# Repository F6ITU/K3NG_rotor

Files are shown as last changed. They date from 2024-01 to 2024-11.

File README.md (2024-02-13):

# K3NG_rotor
Yet another K3NG rotator controler pcb

This implementation is based on an Arduino Mega board and a pair of 4x relay boards to drive an AZ-EL antenna system.

Most basic functions are directly driven via Molex KK 254 connectors (up/down, right/left, lcd display output, GPS input, *
I2C extensions... etc). All other "vacant" gpio could be used via solderpads. 

Board could be powered from 8 to 15V 

Source code and wiki should be downloaded at 

https://github.com/k3ng/k3ng_rotator_controller

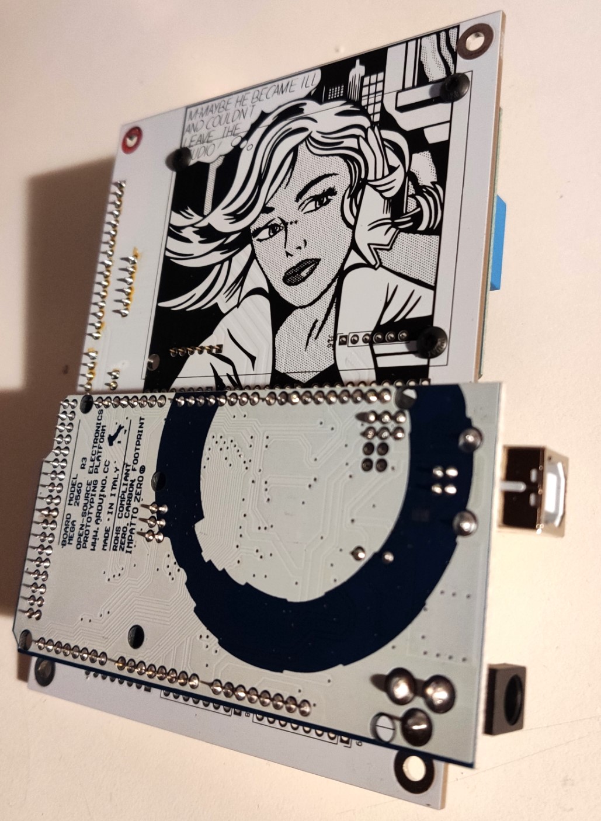
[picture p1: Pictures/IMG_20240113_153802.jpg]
K3NG rotator, component side


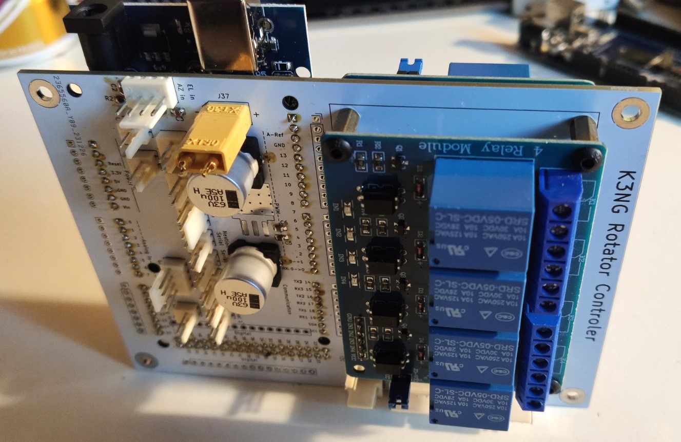
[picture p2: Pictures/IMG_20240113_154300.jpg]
K3NG rotator, bottom side


# Notes de montage

* Les barrettes de contact au pas de 2,54 doivent être soudées après les avoir insérées dans les connecteur gpio de l’Arduino. La série de brasure doit donc être effectuée avec le module MCU en place, lequel servira ainsi de gabarit d’alignement pour les broches. Sans cette précaution, il sera quasiment impossible d’installer l’Arduino sur la carte. 

* Le régulateur de tension doit être le circuit à souder avant tout autre composant. Les deux principaux condensateurs de filtrage sont très proche du 7805 et gêneraient la brasure ce celui-ci s’il était monté a posteriori

* Tous les connecteurs Molex kk254 ne sont pas nécessairement à installer. C’est le cas notamment des entrées gpio « serial » de 0 à 3, qui peuvent être remplacés par de simples jumpers les reliant aux sorties des périphériques installés. Cela permet de choisir sur quel port seront reliés les modules  gps ou Nextion s’il y a lieu

* Toutes les E/S de l’Arduino sont doublées par une rangée de contacts au pas de 2,54, laissant libre toute possibilité d’ajouts de modules exotiques. 

* Les modules « 4 relais » disponibles sur Amazon ou AliExpress sont généralement livrés avec un connecteur « broches  carte à fils » au pas de 2,54mm orientés vers le dessus de la carte. Il est nécessaire de les dessouder et de les remplacer par un connecteur identique, mais soudé « coté piste ». Le shield K3NG doit, pour sa part, être équipé d’un connecteur femelle « carte à carte » pour recevoir la ou les cartes relais en « piggy back ». 

* Deux cartes relais peuvent être installées pour piloter une paire de moteurs azimut/élévation. Prévoir deux entretoises d’une hauteur équivalente aux connecteurs de liaison. 

* ATTENTION : les relais sont commandés « 2 à 2 », soit pour assurer une coupure courants forts, soit pour être utilisés en inverseur (un contact ouvert et un contact fermé au repos, et lycée de Versailles au travail). Cette configuration est notamment nécessaire pour commander les rotor Kantronic/Yaesu/Toyomura d’ancienne génération (split phase ou à phase divisée)

 * Une BOM interactive est disponible sur ce Github dans le répertoire BOM du même métal

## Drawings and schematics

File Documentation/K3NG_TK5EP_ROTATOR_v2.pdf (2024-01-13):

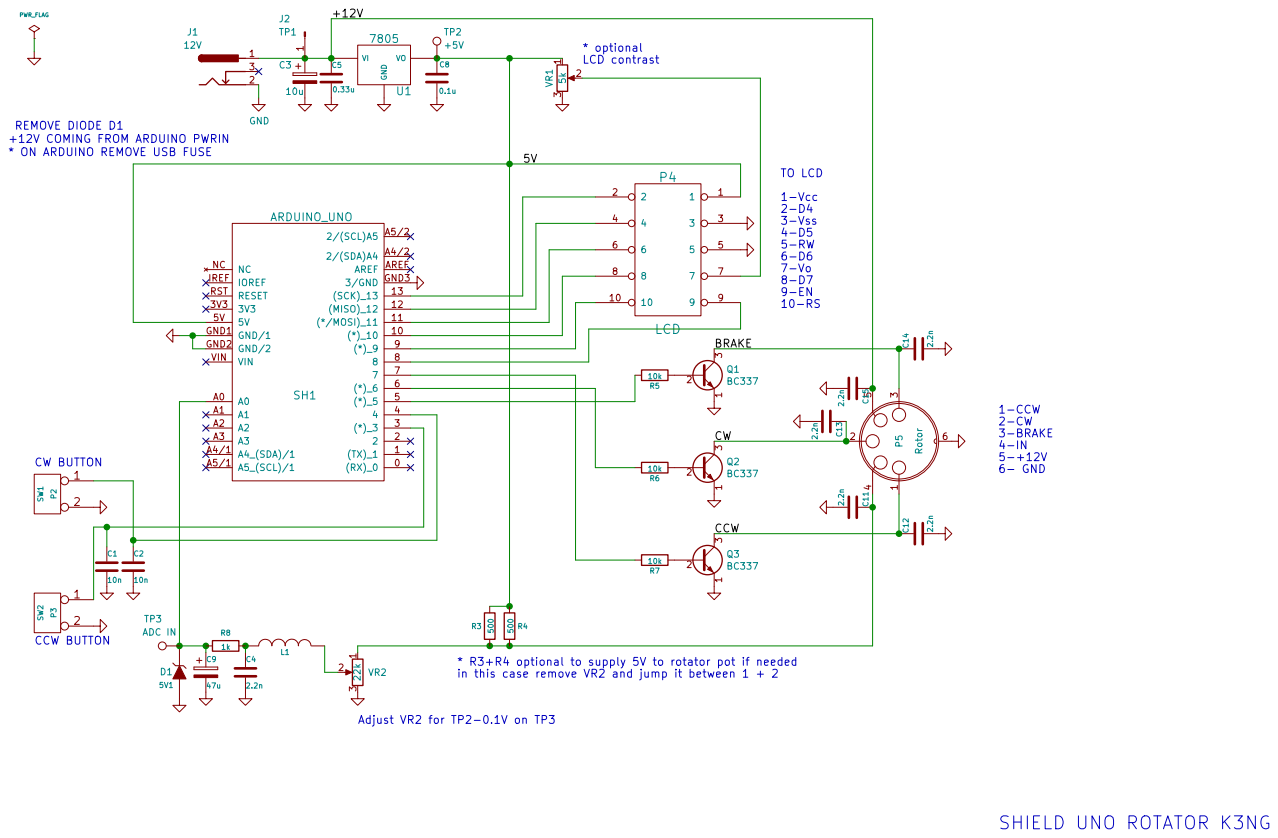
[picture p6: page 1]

+12V COMING FROM ARDUINO PWRIN
* ON ARDUINO REMOVE USB FUSE

ARDUINO_UNO

in this case remove VR2 and jump it between 1 + 2

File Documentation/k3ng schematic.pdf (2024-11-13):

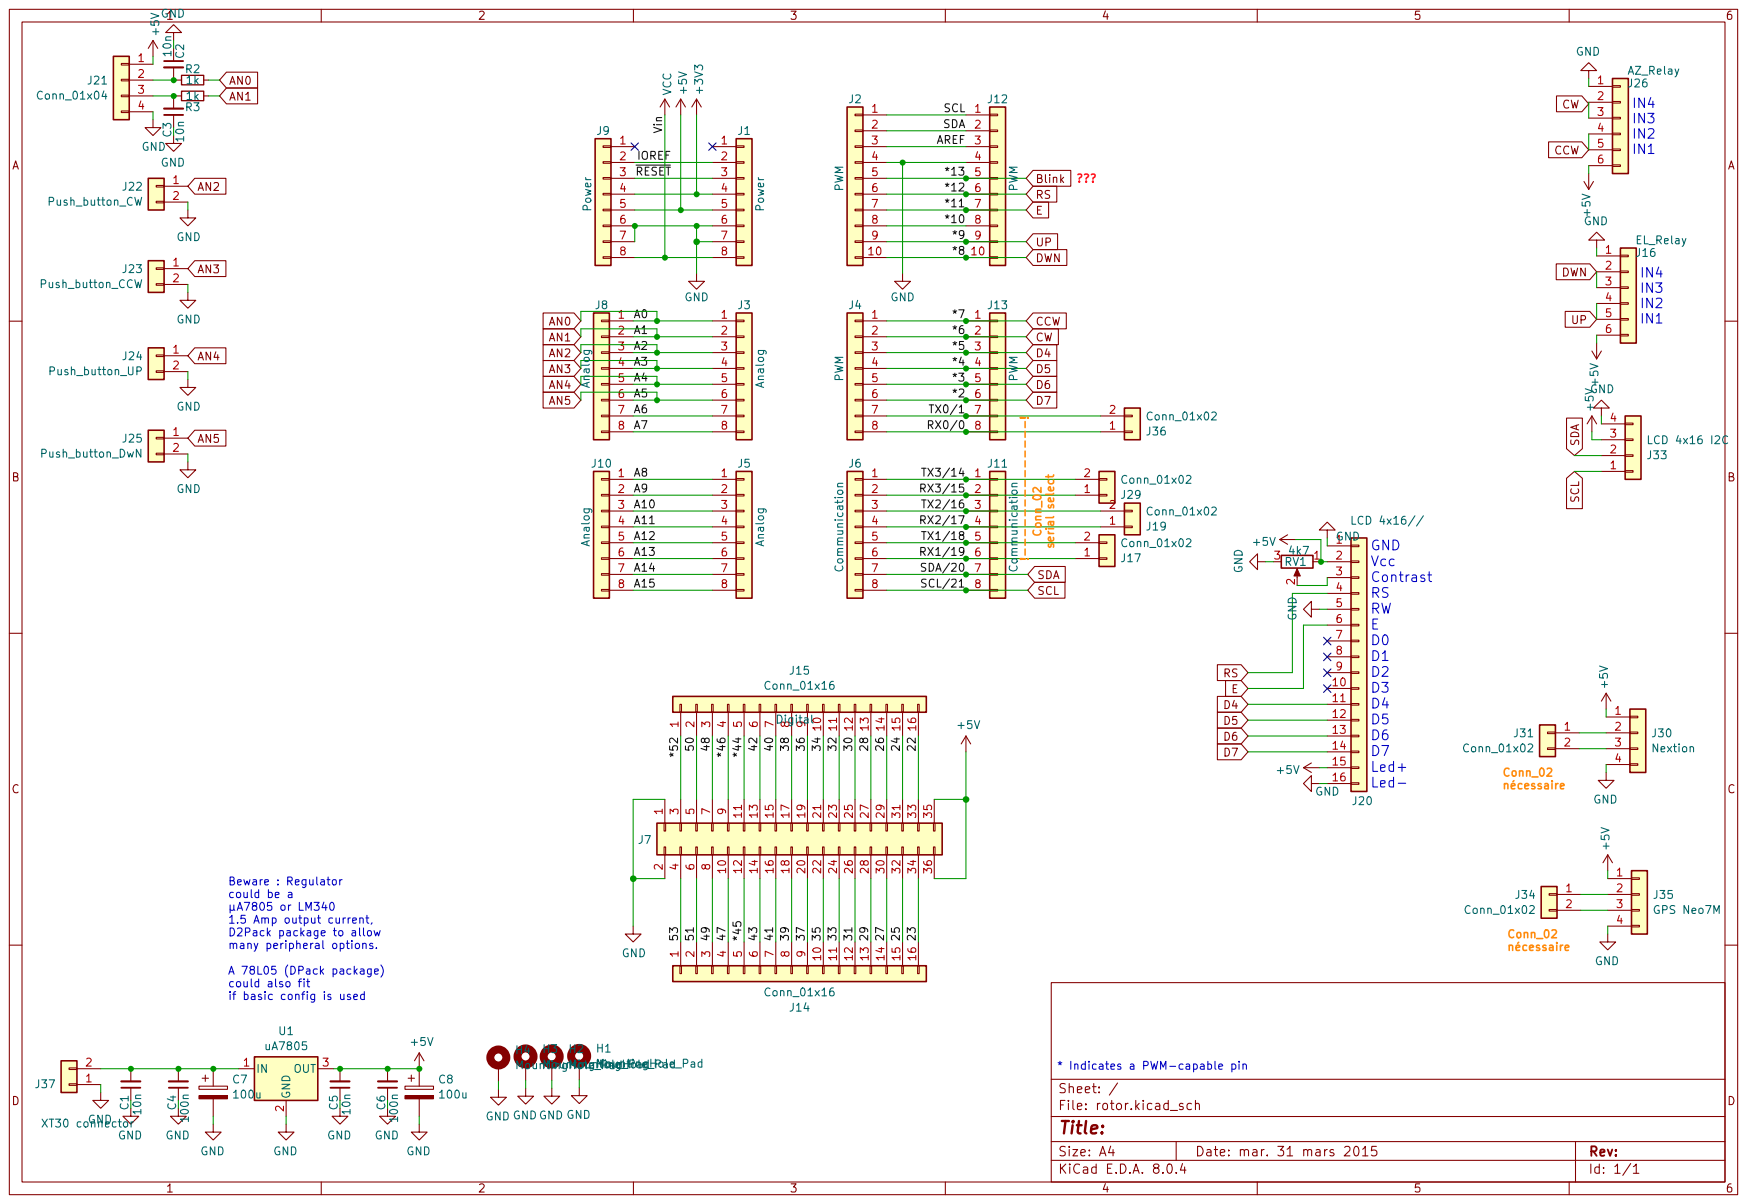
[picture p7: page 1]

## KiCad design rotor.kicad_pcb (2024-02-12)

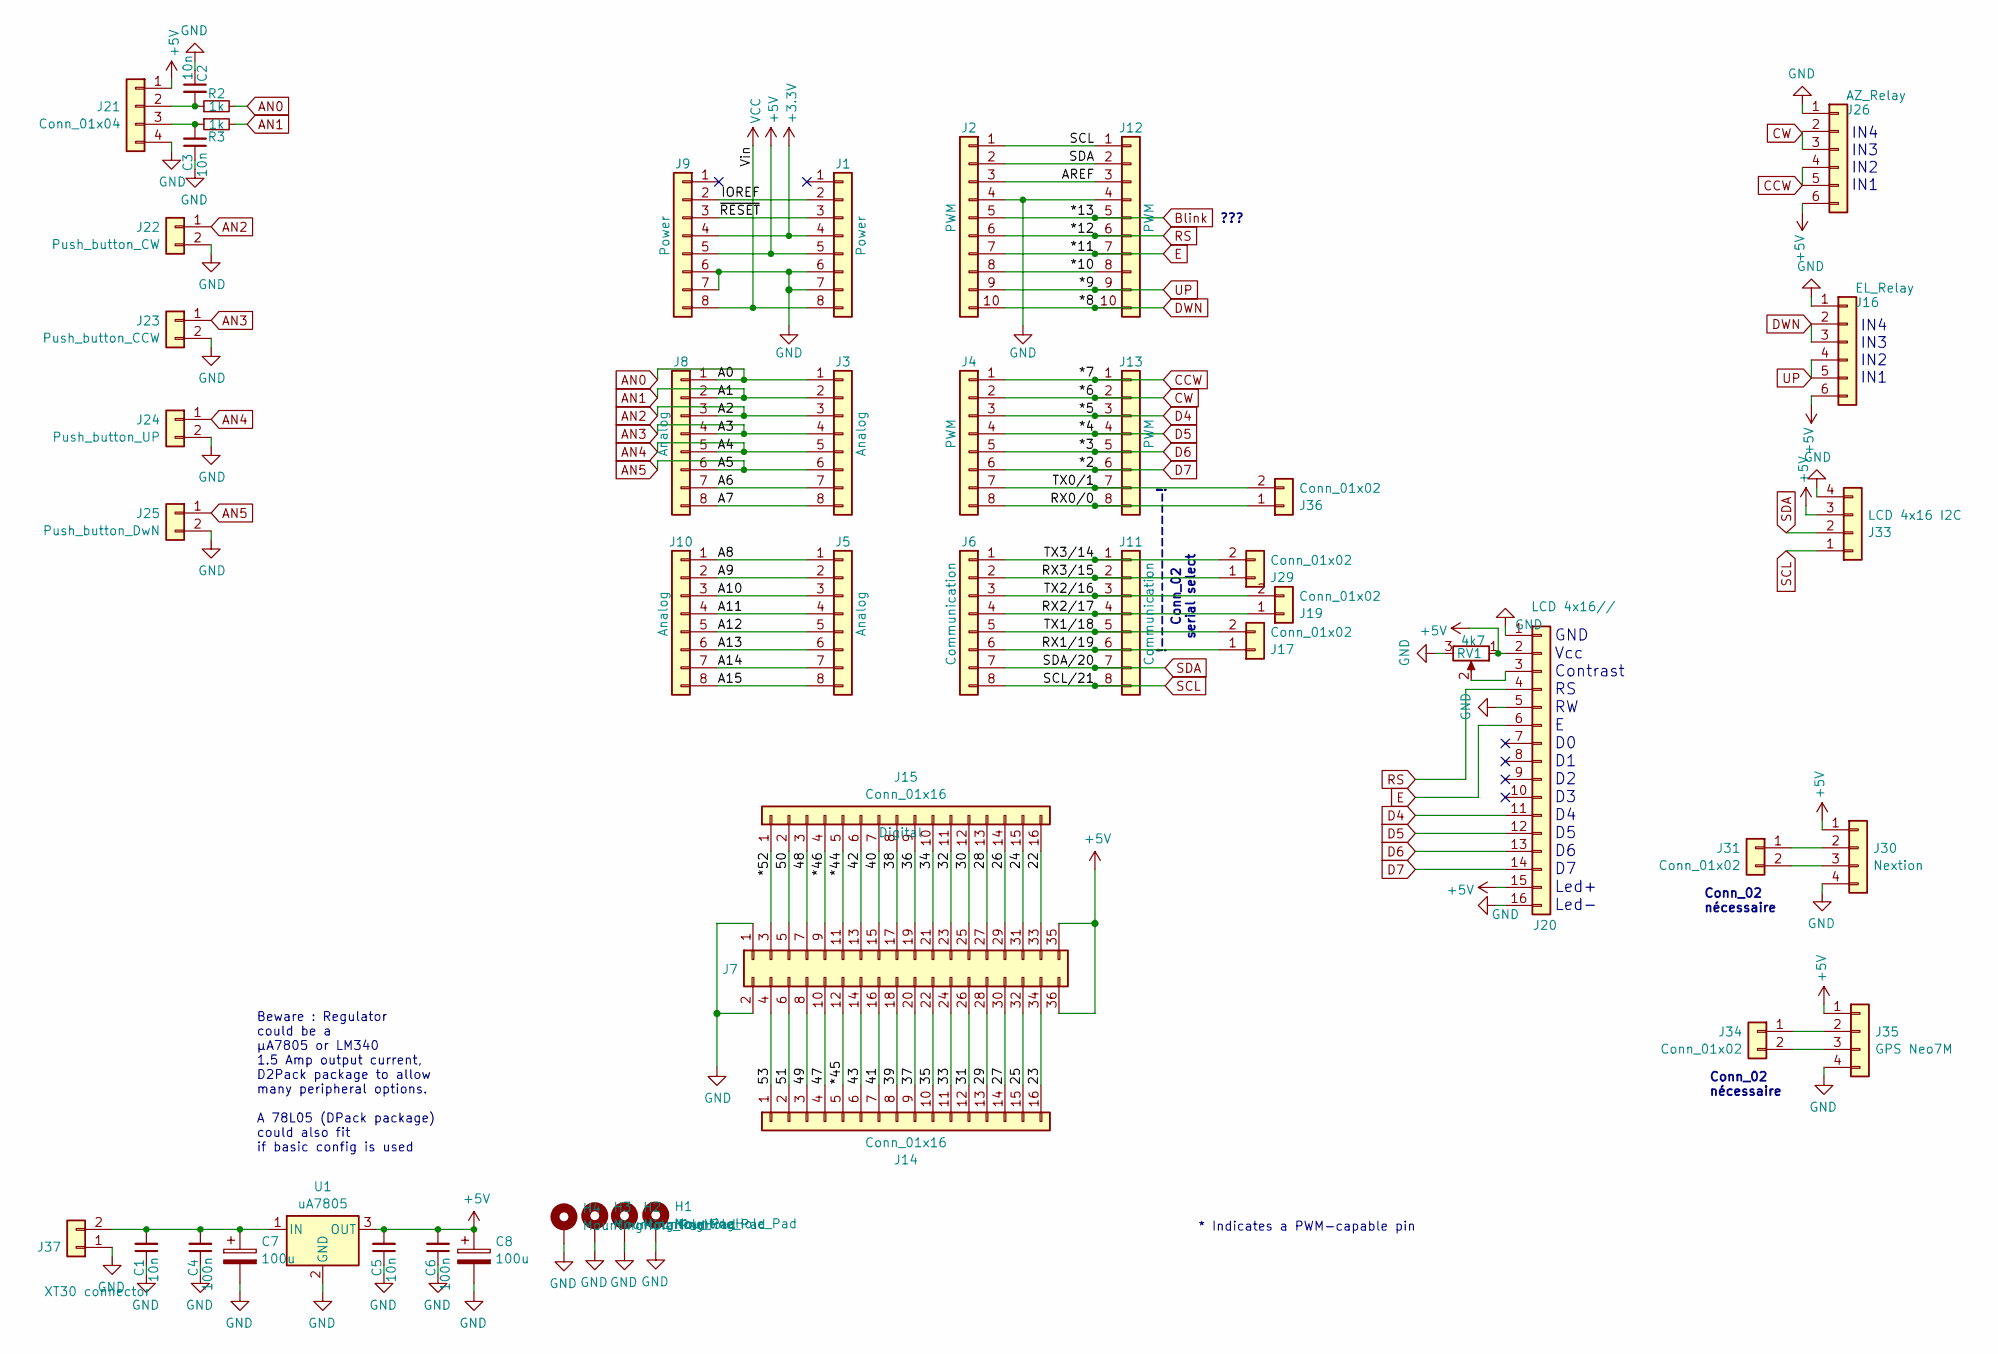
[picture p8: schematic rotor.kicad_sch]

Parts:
C1, C2, C3, C5: 10n; C_0805_2012Metric_Pad1.18x1.45mm_HandSolder
C4, C6: 100n; C_0805_2012Metric_Pad1.18x1.45mm_HandSolder
C7, C8: 100u; CP_Elec_10x12.6
H1, H2, H3, H4: MountingHole_Pad; MountingHole_3.5mm_Pad
J1, J9: Power; PinSocket_1x08_P2.54mm_Vertical
J2, J12: PWM; PinSocket_1x10_P2.54mm_Vertical
J3, J8: Analog; PinHeader_1x08_P2.54mm_Vertical
J4, J13: PWM; PinSocket_1x08_P2.54mm_Vertical
J5, J10: Analog; PinSocket_1x08_P2.54mm_Vertical
J6, J11: Communication; PinSocket_1x08_P2.54mm_Vertical
J7: Digital; PinSocket_2x18_P2.54mm_Vertical
J14, J15: Conn_01x16; PinHeader_1x16_P2.54mm_Vertical
J16: EL_Relay; PinSocket_1x06_P2.54mm_Vertical
J17, J19, J29, J31, J34, J36: Conn_01x02; Molex_KK-254_AE-6410-02A_1x02_P2.54mm_Vertical
J20: LCD 4x16//; Molex_KK-254_AE-6410-16A_1x16_P2.54mm_Vertical
J21: Conn_01x04; Molex_KK-254_AE-6410-04A_1x04_P2.54mm_Vertical
J22: Push_button_CW; Molex_KK-254_AE-6410-02A_1x02_P2.54mm_Vertical
J23: Push_button_CCW; Molex_KK-254_AE-6410-02A_1x02_P2.54mm_Vertical
J24: Push_button_UP; Molex_KK-254_AE-6410-02A_1x02_P2.54mm_Vertical
J25: Push_button_DwN; Molex_KK-254_AE-6410-02A_1x02_P2.54mm_Vertical
J26: AZ_Relay; PinSocket_1x06_P2.54mm_Vertical
J30: Nextion; Molex_KK-254_AE-6410-04A_1x04_P2.54mm_Vertical
J33: LCD 4x16 I2C; Molex_KK-254_AE-6410-04A_1x04_P2.54mm_Vertical
J35: GPS Neo7M; Molex_KK-254_AE-6410-04A_1x04_P2.54mm_Vertical
J37: XT30 connector; AMASS_XT30U-F_1x02_P5.0mm_Vertical
R2, R3: 1k; R_0805_2012Metric_Pad1.20x1.40mm_HandSolder
RV1: 4k7; Potentiometer_Bourns_TC33X_Vertical
U1: uA7805; TO-263-3_TabPin2

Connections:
+3V3: J1.4, J9.4
+5V: C5.2, C6.2, C8.1, J1.5, J7.35, J7.36, J9.5, J16.6, J20.2, J20.15, J21.1, J26.6, J30.1, J33.3, J35.1, RV1.1, U1.3 (OUT)
/22: J7.33, J15.16
/23: J7.34, J14.16
/24: J7.31, J15.15
/25: J7.32, J14.15
/26: J7.29, J15.14
/27: J7.30, J14.14
/28: J7.27, J15.13
/29: J7.28, J14.13
/30: J7.25, J15.12
/31: J7.26, J14.12
/32: J7.23, J15.11
/33: J7.24, J14.11
/34: J7.21, J15.10
/35: J7.22, J14.10
/36: J7.19, J15.9
/37: J7.20, J14.9
/38: J7.17, J15.8
/39: J7.18, J14.8
/40: J7.15, J15.7
/41: J7.16, J14.7
/42: J7.13, J15.6
/43: J7.14, J14.6
/47: J7.10, J14.4
/48: J7.7, J15.3
/49: J7.8, J14.3
/50: J7.5, J15.2
/51: J7.6, J14.2
/53: J7.4, J14.1
/*10: J2.8, J12.8
/*44: J7.11, J15.5
/*45: J7.12, J14.5
/*46: J7.9, J15.4
/*52: J7.3, J15.1
/A6: J3.7, J8.7
/A7: J3.8, J8.8
/A8: J5.1, J10.1
/A9: J5.2, J10.2
/A10: J5.3, J10.3
/A11: J5.4, J10.4
/A12: J5.5, J10.5
/A13: J5.6, J10.6
/A14: J5.7, J10.7
/A15: J5.8, J10.8
/AREF: J2.3, J12.3
/IOREF: J1.2, J9.2
/RX0/0: J4.8, J13.8, J36.1
/RX1/19: J6.6, J11.6, J17.1
/RX2/17: J6.4, J11.4, J19.1
/RX3/15: J6.2, J11.2, J29.1
/TX0/1: J4.7, J13.7, J36.2
/TX1/18: J6.5, J11.5, J17.2
/TX2/16: J6.3, J11.3, J19.2
/TX3/14: J6.1, J11.1, J29.2
/~RESET: J1.3, J9.3
AN0: J3.1, J8.1, R2.2
AN1: J3.2, J8.2, R3.2
AN2: J3.3, J8.3, J22.1
AN3: J3.4, J8.4, J23.1
AN4: J3.5, J8.5, J24.1
AN5: J3.6, J8.6, J25.1
Blink: J2.5, J12.5
CCW: J4.1, J13.1, J26.4, J26.5
CW: J4.2, J13.2, J26.2, J26.3
D4: J4.3, J13.3, J20.11
D5: J4.4, J13.4, J20.12
D6: J4.5, J13.5, J20.13
D7: J4.6, J13.6, J20.14
DWN: J2.10, J12.10, J16.2, J16.3
E: J2.7, J12.7, J20.6
GND: C1.1, C2.1, C3.1, C4.1, C5.1, C6.1, C7.2, C8.2, H1.1, H2.1, H3.1, H4.1, J1.6, J1.7, J2.4, J7.1, J7.2, J9.6, J9.7, J12.4, J16.1, J20.1, J20.5, J20.16, J21.4, J22.2, J23.2, J24.2, J25.2, J26.1, J30.4, J33.4, J35.4, J37.1, RV1.3, U1.2 (GND)
unnamed: J20.3, RV1.2
unnamed: C2.2, J21.2, R2.1
unnamed: C3.2, J21.3, R3.1
unnamed: J30.2, J31.1
unnamed: J30.3, J31.2
unnamed: J34.1, J35.2
unnamed: J34.2, J35.3
unnamed: C1.2, C4.2, C7.1, J37.2, U1.1 (IN)
RS: J2.6, J12.6, J20.4
SCL: J2.1, J6.8, J11.8, J12.1, J33.1
SDA: J2.2, J6.7, J11.7, J12.2, J33.2
UP: J2.9, J12.9, J16.4, J16.5
VCC: J1.8, J9.8

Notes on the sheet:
???
IN4 IN3 IN2 IN1
!--------------! Conn_02 serial select
Conn_02 nécessaire
GND Vcc Contrast RS RW E D0 D1 D2 D3 D4 D5 D6 D7 Led+ Led-
* Indicates a PWM-capable pin
Beware : Regulator could be a µA7805 or LM340 1.5 Amp output current, D2Pack package to allow many peripheral options. A 78L05 (DPack package) could also fit if basic config is used

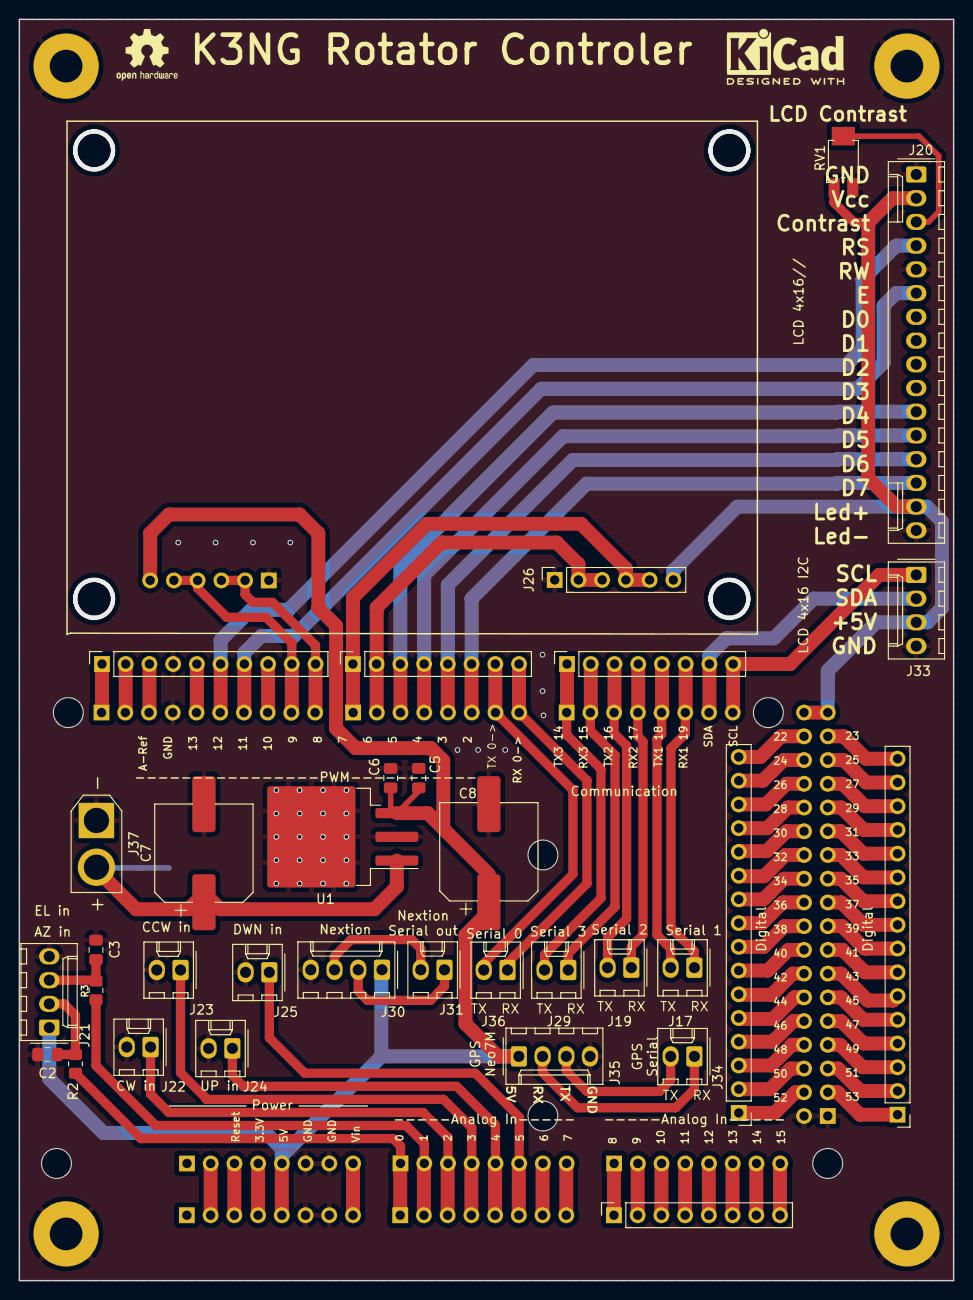
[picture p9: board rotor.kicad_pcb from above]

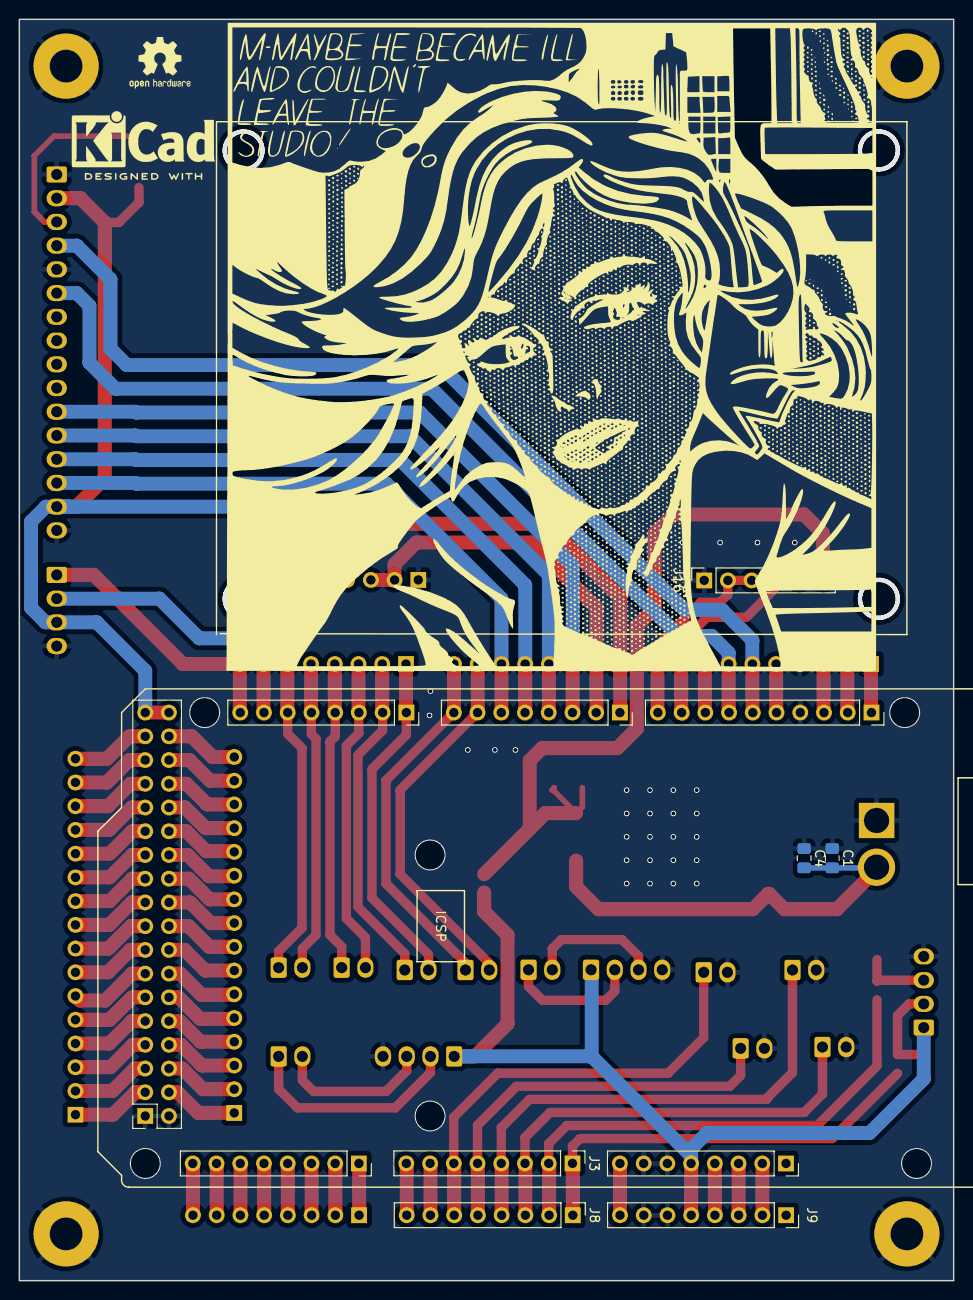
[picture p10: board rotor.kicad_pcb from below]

Board: 2 copper layers, 100.0 x 135.0 mm, 55 parts (12 on the bottom side), 85 nets.

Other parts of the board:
MH1, MH2, MH3, MH4, MH5, MH6: MountingHole_3.2mm

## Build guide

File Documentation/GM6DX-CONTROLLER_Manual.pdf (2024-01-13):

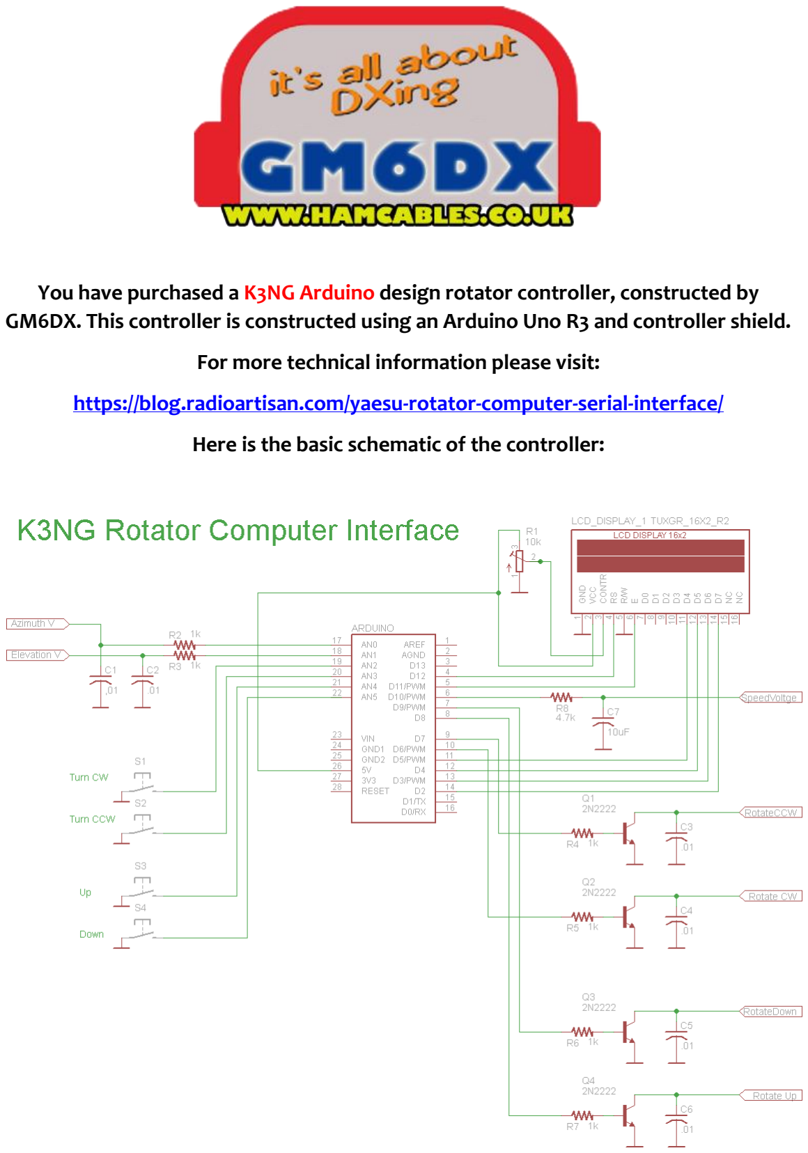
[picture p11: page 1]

You have purchased a K3NG Arduino design rotator controller, constructed by GM6DX. This controller is constructed using an Arduino Uno R3 and controller shield.

For more technical information please visit:

https://blog.radioartisan.com/yaesu-rotator-computer-serial-interface/

Here is the basic schematic of the controller:

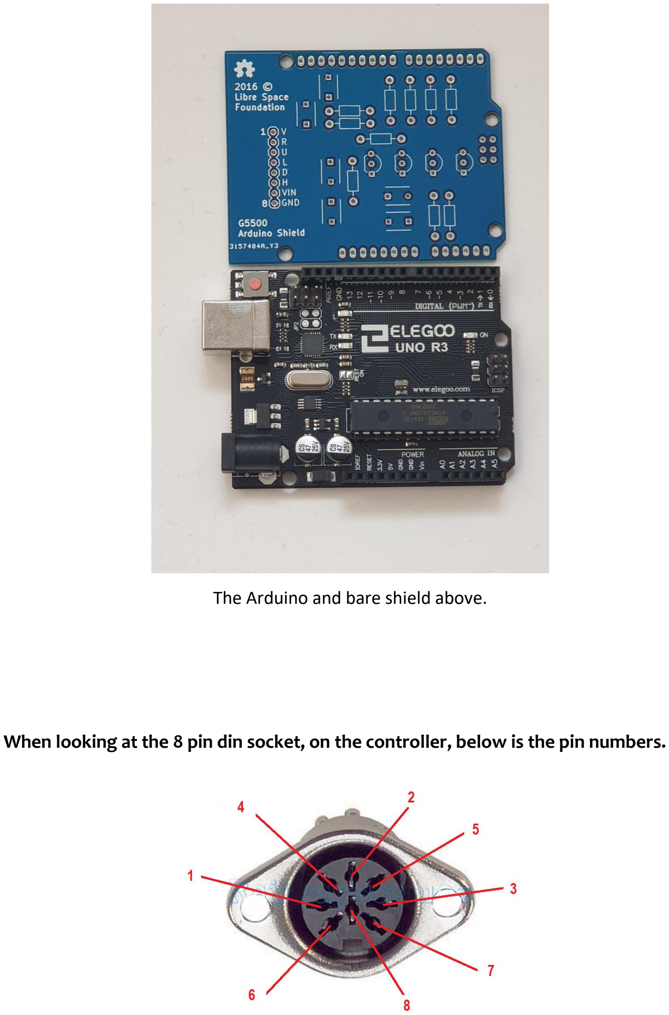
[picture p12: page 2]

The Arduino and bare shield above.

When looking at the 8 pin din socket, on the controller, below is the pin numbers.

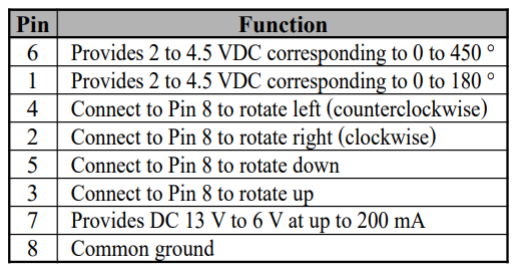
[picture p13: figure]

This controller works when used with the correct software. The software which I know works very well and has numerous options of different types of controllers is PST rotator software available here:

https://www.qsl.net/yo3dmu/index_Page346.htm

The Arduino Uno drivers should install automatically when connected to the PC, if they don’t they can be found here:

http://www.mediafire.com/file/pk38wysr26mak2f/CH341SER.rar/file

Or search for your own, it uses the CH340 chip set.

- If you are using this controller for a Yaesu G5500 then just use a standard straight through 8 pin din to 8 pin din cable.
- If you are using this controller for a Yaesu controller which has a 6 pin mini din on the rear (such as the G1000 etc) then please use the supplied cable.
8 PIN DIN | 6 PIN MINI DIN
2 ----------------------------------------------------------------------1 4----------------------------------------------------------------------2 6----------------------------------------------------------------------4 8----------------------------------------------------------------------5
| 3 & 6 (Soldered together)
- If you are looking to use this on another rotator then please refer to the pin out above.

Step 1 – Plug the USB to USB-B cable into the controller and into the PC.

You will see a red light on, indicating that the Arduino board is connected to the PC and is powered.

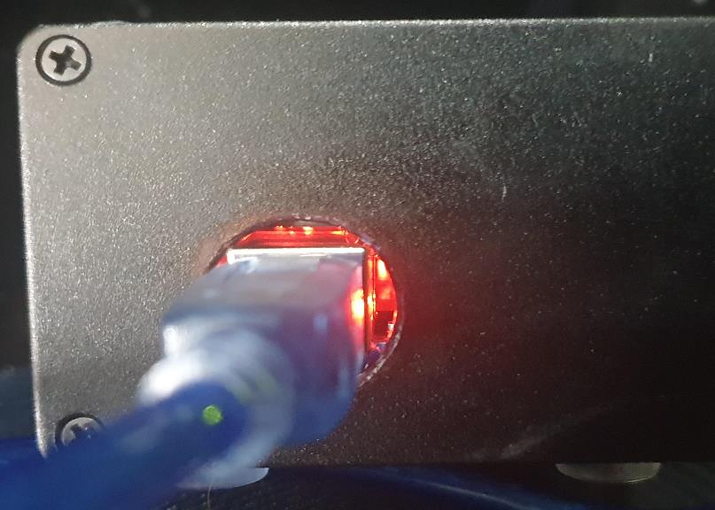
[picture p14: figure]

Note the circle cut out allows air to flow into the enclosure enough to keep the board cool during operation.

If you do not see a red light, check your USB cable.

Step 2 – Let your PC install the drivers or have the drivers installed onto your PC via the link above.
Step 3 – Set up your controller software for the Arduino K3NG design.

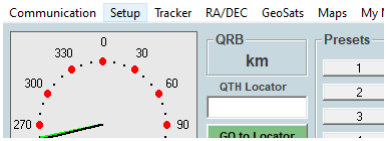
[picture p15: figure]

Select Setup

Select AZ Controller

Select K3NG Arduino (or you can select GS-232 450 deg – as the controller is a Yaesu clone)

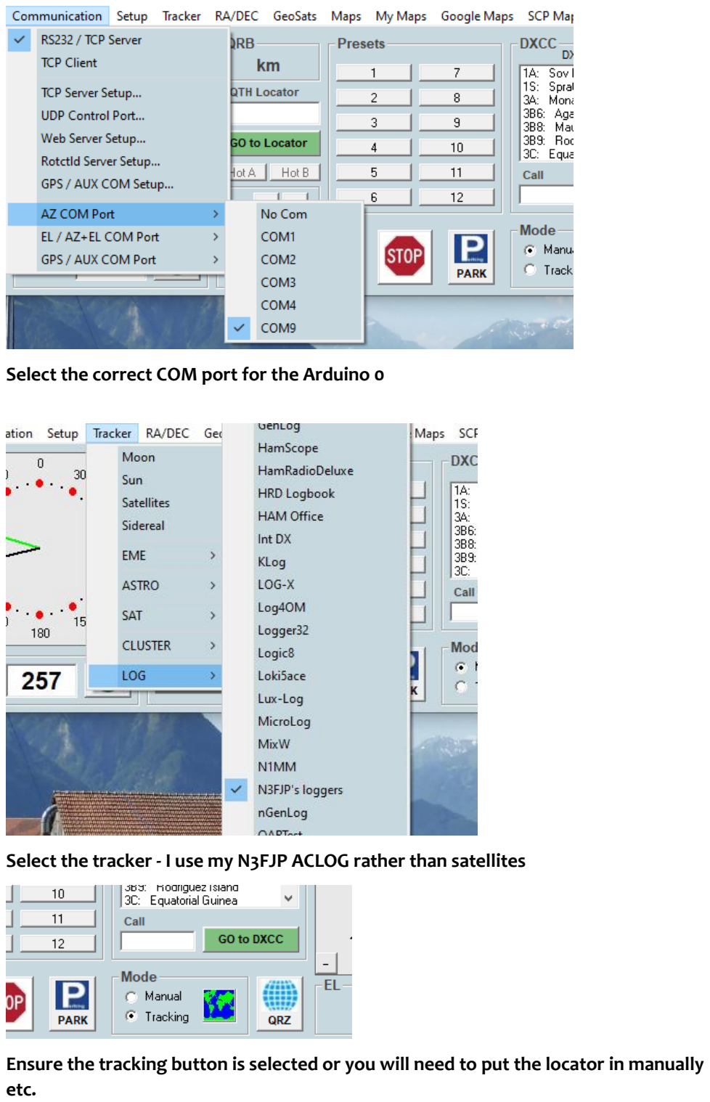
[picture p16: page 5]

Select the correct COM port for the Arduino 0

Select the tracker - I use my N3FJP ACLOG rather than satellites

Ensure the tracking button is selected or you will need to put the locator in manually etc.

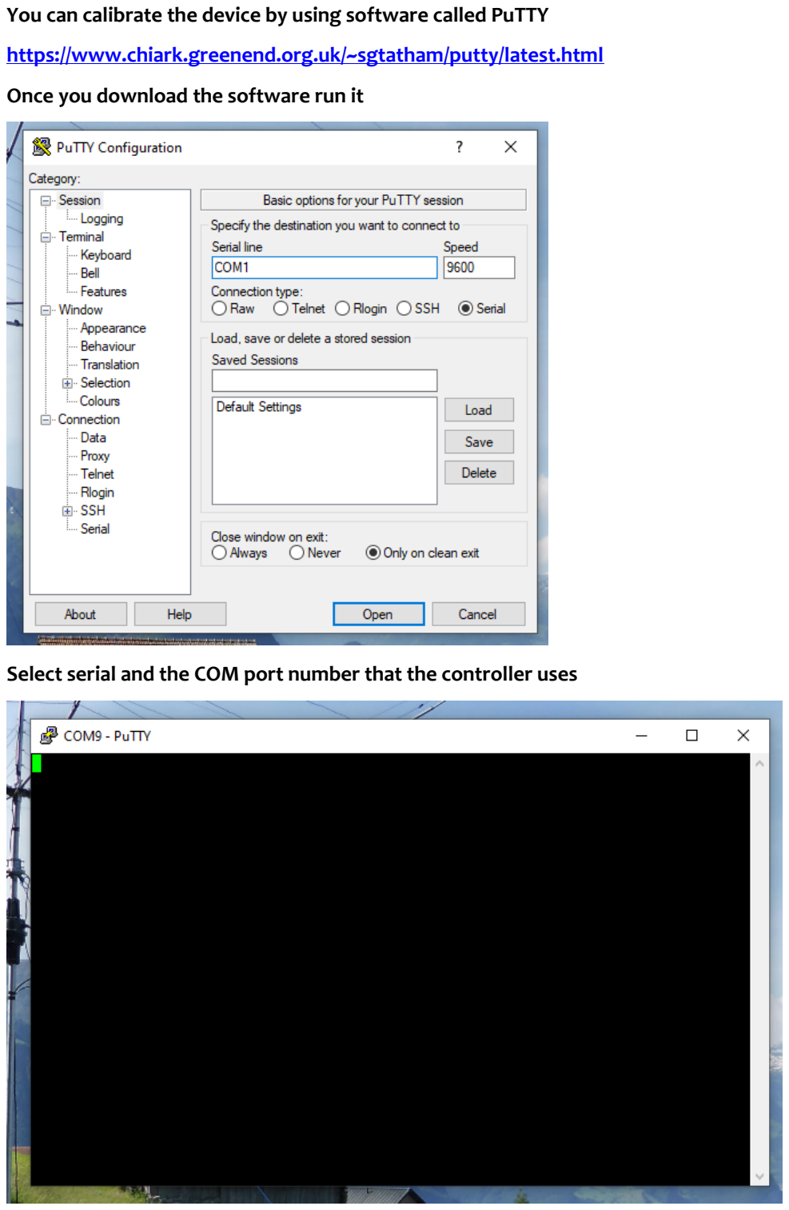
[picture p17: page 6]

You can calibrate the device by using software called PuTTY

https://www.chiark.greenend.org.uk/~sgtatham/putty/latest.html

Once you download the software run it

Select serial and the COM port number that the controller uses

Then use the following commands

C

Then you will get a reading something like

Then press F it will tell you to turn the rotator all the way clockwise

Then it will say wrote to memory

Then press O it will tell you to turn the rotator all the way counter clock wise

Then press Enter

That should be you done

FULL LIST OF COMMANDS FOR PUTTY BELOW:

B | - Report elevation
C | - Report azimuth
C2 | - Report azimuth and elevation
S | - Stop all rotation
A | - Stop azimuth rotation
E | - Stop elevation rotation
L | - Rotate azimuth left (CCW)
R | - Rotate azimuth right (CW)
D | - Rotate elevation down
U | - Rotate elevation up
Mxxx | - Move to azimuth
Wxxx yyy | - Move to azimuth xxxx and elevation yyy
X1 | - Change to azimuth rotation speed setting 1
X2 | - Change to azimuth rotation speed setting 2
X3 | - Change to azimuth rotation speed setting 3
X4 | - Change to azimuth rotation speed setting 4
O | - Azimuth offset calibration
F | - Azimuth full scale calibration
O2 | - Elevation offset calibration
F2 | - Elevation full scale calibration
P36 | - Switch to 360 degree mode
P45 | - Switch to 450 degree mode
Z | - Toggle north / south centered mode
H | - Help

You can also go SETUP > ANTENNA OFFSET

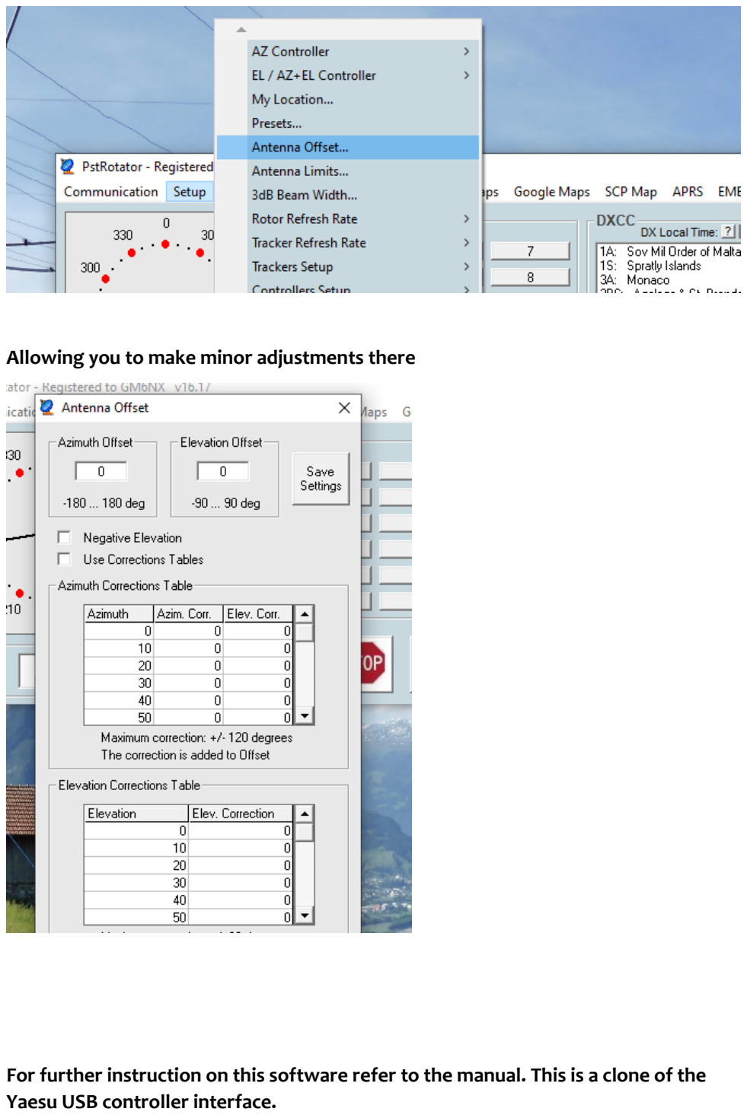
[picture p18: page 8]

Allowing you to make minor adjustments there

For further instruction on this software refer to the manual. This is a clone of the Yaesu USB controller interface.

The controller is constructed from an aluminium enclosure reducing RFI concerns it also has 4 large rubber feed to ensure it does not scratch any of your surfaces.

I test every unit to ensure they work prior to shipping.

Any further questions please ask

gm6dx@outlook.com

Thanks

# GM6DX

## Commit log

2024-01-13 initial release and prototype. Gerber and iBom should be ok
    [rotor-B_Cu.gbl, rotor-B_Mask.gbs, rotor-B_Paste.gbp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]
2024-02-12 minor fixes, new iBom, RTM version
    [rotor-B_Cu.gbl, rotor-B_Mask.gbs, rotor-B_Paste.gbp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]
2024-11-13 updated schematic pdf
    [rotor.kicad_sch]
